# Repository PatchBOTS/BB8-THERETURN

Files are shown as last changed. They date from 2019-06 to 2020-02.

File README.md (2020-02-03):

# BB8-THERETURN
In March 2019 I decided to rebuild my James Bruton V3 BB-8 electronics from the ground up. Here are my Results. 

I've posted the zipped Gerber files for the board. This can be uploading directly to PCBWay.com or other board house for fabrication. 
I've also posted a CSV for the digikey passive components needed to assemble the board.  
Here is a link to the digikey BOM (let me know if this isn't working)
https://www.digikey.com/BOM/Create/CreateSharedBom?bomId=8143564

Notes on Assembly. 
1. To make room on the board I only have through holes for the needed pins on both the Sparkfun Pro Micro and the BY8301-16p.  This means you will NOT be soldering all the pin headers onto the Sparkfun Pro Micro and you will need to CUT pins off of the BY8301-16p.  This also makes it a bit lighter :)
2. There is a built in programming port for the HC-05 module on the board. I recommend soldering the HC-05 module on first and using this programming port to get your Slave Binding address before continuing with assembly. 
3. There is mP3 solder jumper underneath the BY8301-16p labled "mp3 program"  you will need to solder this jumper for the board to work.  You will need to unsolder it to reprogram the mp3 player after installation. 

I Wil update this guide with pictures as soon as possible. Feel free to message me in the meantime with any questions.

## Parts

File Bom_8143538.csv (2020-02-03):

Manufacturer Part Number | Manufacturer | Digi-Key Part Number | Customer Reference | Reference Designator | Packaging | Part Status | Quantity | Unit Price | Extended Price | Quantity Available | Mfg Std Lead Time | Description | RoHS Status | Lead Free Status | REACH Status
L6932H1.2TR | STMicroelectronics | 497-7766-1-ND |  |  | Cut Tape (CT) | Active | 2 | 2.80000 | $5.60 | 7 | 11 Weeks | IC REG LINEAR POS ADJ 2A 8HSO | ROHS3 Compliant | Lead free | REACH Unaffected
C4532JB1C226M200KA | TDK Corporation | 445-11945-1-ND |  |  | Cut Tape (CT) | Active | 4 | 1.30000 | $5.20 | 1376 | 12 Weeks | CAP CER 22UF 16V JB 1812 | ROHS3 Compliant | Lead free | REACH Unaffected
ERJ-12ZYJ104U | Panasonic Electronic Components | P100KWCT-ND |  |  | Cut Tape (CT) | Active | 2 | 0.26000 | $0.52 | 4887 | 13 Weeks | RES SMD 100K OHM 5% 3/4W 2010 | ROHS3 Compliant | Lead free | REACH Unaffected
RC2010JK-071KL | Yageo | YAG3385CT-ND |  |  | Cut Tape (CT) | Active | 2 | 0.21000 | $0.42 | 85407 | 33 Weeks | RES SMD 1K OHM 5% 3/4W 2010 | ROHS3 Compliant | Lead free | REACH Unaffected
RMCF2010JT2K00 | Stackpole Electronics Inc | RMCF2010JT2K00CT-ND |  |  | Cut Tape (CT) | Active | 1 | 0.23000 | $0.23 | 14356 | 17 Weeks | RES 2K OHM 5% 3/4W 2010 | ROHS3 Compliant | Lead free | REACH Unaffected
CRCW20103K30FKEF | Vishay Dale | 541-3.30KACCT-ND |  |  | Cut Tape (CT) | Active | 1 | 0.29000 | $0.29 | 11927 | 12 Weeks | RES SMD 3.3K OHM 1% 3/4W 2010 | ROHS3 Compliant | Lead free | Not Available
ERJ-12ZYJ362U | Panasonic Electronic Components | P3.6KWCT-ND |  |  | Cut Tape (CT) | Active | 1 | 0.26000 | $0.26 | 4770 | 13 Weeks | RES SMD 3.6K OHM 5% 3/4W 2010 | ROHS3 Compliant | Lead free | REACH Unaffected
DEV-12640 | SparkFun Electronics | 1568-1060-ND |  |  | Bulk | Active | 1 | 19.95000 | $19.95 | 234 | 2 Weeks | PRO MICRO ATMEGA32U4 5V/16MHZ | RoHS Compliant | Lead free | Not Available

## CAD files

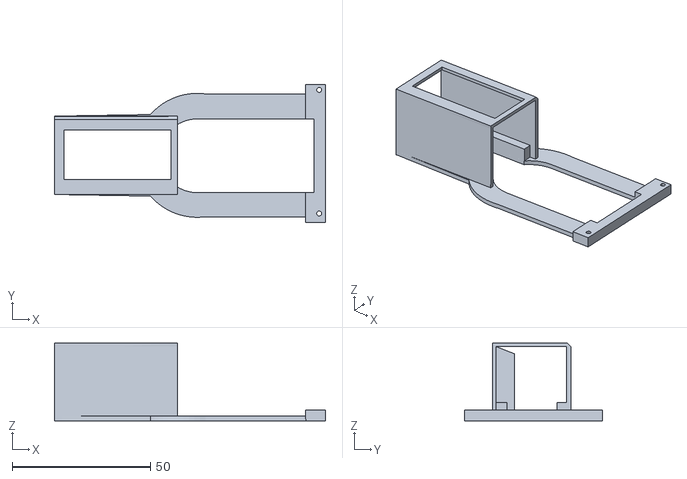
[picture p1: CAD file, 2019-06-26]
InternalSLEDMount.STL
98.0 x 49.7 x 28.0

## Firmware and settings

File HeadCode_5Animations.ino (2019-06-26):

// =======================================================================================
//                         BB-8 Head -- Lights and Sounds
// =======================================================================================
//                            Written By: PatchBOTS
// =======================================================================================
//       Credit and  Major thank you to:  David Scott,  afreeland, and ron_dl
// ---------------------------------------------------------------------------------------
//                     microcontroller  ---  Sparkfun Pro Micro (5v)
// --------------------------------------------------------------------------------------
//
//                                 proMicro
//                                ------------
//                                |           |
//                     +--------------------------------+
//                     |                                |
//                     | [ ]TX                   RAW[ ] |
//              HC-05  | [ ]RX                   GND[ ] |
//                     | [ ]GND                  RST[ ] |
//                     | [ ]GND                  VCC[ ] |
//                     | [ ]2                     A3[ ] |
//               Busy  | [ ]3                     A2[ ] |
//              NeoPix | [ ]4                     A1[ ] |
//               State | [ ]5                     A0[ ] | Audio in
//                     | [ ]6                     15[ ] | SoftSerialTX
//                     | [ ]7                     14[ ] |
//                     | [ ]8                     16[ ] |
//                     | [ ]9                     10[ ] |
//                     |                                |
//                     +--------------------------------+
//
//
// ---------------------------------------------------------------------------------------
//                                   NOTES
// ---------------------------------------------------------------------------------------
//
//SMD HC-05 Bluetooth Module Slave address:  98d3,32,31870f

// -----------------------------------------------------------------------------
//                          Libraries
// -----------------------------------------------------------------------------
#include "MP3FLASH16P.h"
#include <Adafruit_NeoPixel.h>
#include <SoftwareSerial.h>

// -----------------------------------------------------------------------------
//                      Definitions/Variables
// -----------------------------------------------------------------------------

#define mp3busypin 3  // connected to Busy pin on Mp3 Unit
#define AudioIn    A0 //connected to SPK1 on mP3 player
#define neopixel   4  // neopixels out

//**********NeoPixels**************
#define NUMPIXELS      18
Adafruit_NeoPixel pixels = Adafruit_NeoPixel(NUMPIXELS, neopixel, NEO_GRB + NEO_KHZ800);

//*****Arrays for specific NeoLights
int blueLogicArray [] = {0, 1, 2};
int topLogicArray [] = {3, 5, 7};
int bottomLogicArray [] = {4, 6, 8};
int dualLogicArray [] = {3, 4, 5, 6, 7, 8}; //for both top and bottom white logic displays
int dualLogicHoloArray [] = {3, 4, 5, 6, 7, 8, 10}; //for both top and bottom white logics and the hololens
int radarArray [] = {11, 12, 13, 14, 15, 16, 17};
//PSI light is 9
//HoloLens is 10

//**********Serial Input**************
boolean newData = false;
const byte numChars = 32;
char receivedChars[numChars];
char tempChars[numChars];
int trig1 = 1;
int trig2 = 1;
int trig3 = 1;
int trig4 = 1;
int trig5 = 1;
int volumeKnob = 500;
int aniMode = 0;

//**********PSI Light**************
int AudioReading;
int mp3volume;
int voiceBrightness = 0;
int audioUpper;
int audioLower;
int absoluteUpper;
int pulse;

//**********mp3Player**************
MP3FLASH16P myPlayer; //calls the David Scott mp3 library

//**********Timing**************
long previousMillis = 0;        // will store last time sound played was updated
long sound_interval = 15000; //the autonomous sound interval.  15000 = 15 seconds between sounds
int currentMillis = 0;

//*********AnimationVaribales*************************
//GLOBAL
long startTime = 0; //used as a stopwatch for the animations

//Color Variables
uint32_t low = pixels.Color(0, 0, 0); //a simple way of writing "turn this pixel off"
uint32_t neoRed = pixels.Color(255, 0, 0);//a simple way of writing "turn this pixel red"
uint32_t neoBlue = pixels.Color(0, 0, 255);//a simple way of writing "turn this pixel blue"
uint32_t neoWhite = pixels.Color(255, 255, 255);//a simple way of writing "turn this pixel white"
uint32_t voiceBright = pixels.Color(voiceBrightness, voiceBrightness, voiceBrightness); //a simple way of writing "make this pixel match teh voice brightness"
uint32_t voiceBrightRed = pixels.Color(voiceBrightness,0,0); //a simple way of writing "make this pixel match teh voice brightness in a red color"
uint32_t voiceBrightBlue = pixels.Color(0,0,voiceBrightness); //a simple way of writing "make this pixel match teh voice brightness in a Blue color"

//Animation 1
int aniOneInterval = 60; //for single knightriders, time between each lightup
int aniOne_i = 0; //generic holder
int aniOne_iLast = 0;
int aniOneRiderFlag = 3; //this will allow the loops of knightrider scrolls to run sequentially
unsigned long aniOneMillis = 0;  //local stopwatch for Animation 1
long aniOnePreviousMillis = 0; //a ref point for timing
bool aniOneP2 = false; 

//Animation 2
unsigned long aniTwoMillis = 0;  //local stopwatch for Animation 1
bool aniTwoFlag1= false; 
bool aniTwoFlag2= false; 
bool aniTwoFlag3= false;
bool aniTwoFlag4= false;
bool aniTwoFlag5= false; 
int aniTwo_i = 0; //generic holder
int aniTwo_iLast = 0;
int aniTwoRiderFlag = 0; //this will allow the loops of knightrider scrolls to run sequentially
int aniTwoInterval = 60; //for single knightriders, time between each lightup
long aniTwoPreviousMillis = 0; //a ref point for timing

//Animation 3
unsigned long aniThreeMillis = 0;  //local stopwatch for Animation 1
long aniThreePreviousMillis = 0; //a ref point for timing
bool aniThreeFlag = false; 

//Animation 4
unsigned long aniFourMillis = 0;  //local stopwatch for Animation 1
long aniFourPreviousMillis = 0; //a ref point for timing
bool aniFourFlag = false; 

//Animation 5
unsigned long aniFiveMillis = 0;  //local stopwatch for Animation 1
long aniFivePreviousMillis = 0; //a ref point for timing
bool aniFiveFlag = false; 



// -----------------------------------------------------------------------------
//                              SETUP
// -----------------------------------------------------------------------------
void setup() {
  myPlayer.init(mp3busypin);   // Init the player with the busy pin connected to Arduino pin 3
  delay(1000);  // Startup delay
  Serial.begin(9600);  //Start Serial, eventually connecting to HC-05
  Serial1.begin(9600);
  pixels.begin(); // This initializes the NeoPixel library.
  pinMode(AudioIn, INPUT); //set pin to read voltage output
 knightRider();

}
// -----------------------------------------------------------------------------
//                             MAIN LOOP
// -----------------------------------------------------------------------------
void loop() {
  currentMillis = millis();

  serialStuff(); //reads and parses all incoming serial data into integers.  there is an function "showParsedData" which will print to Serial Monitor for debugging

  //**********Volume Knob************************
  mp3volume = map(volumeKnob, 0, 1023, 0, 30); //reads and scales the poteniometer value (0-1023) to a usable mp3 volume (0-30)
  psiLightData (); //this function calculates the light value for the PSI based on the volumeKnob value.

  neoPixels(); //default NeoPixels values for the droid.  Animations will potential update these values before they are shown in the trigModeAni function below
  autoMode(); // This will play a random sound at the desired interval. To change look for "long sound_interval" under "Timing"
  trigMode(); //This will play a sound triggered by the buttons when Animation Mode is not engaged.
  trigModeAni(); //This will play a sound triggered by the buttons with Animations when Animation Mode is engaged.

  aniOne();
  aniTwo();
  aniThree();
  aniFour(); 
  aniFive();

  pixels.show(); // This sends the updated pixel color to the hardware.

}



// -----------------------------------------------------------------------------
//                ADDITIONAL FUNCTIONS (NON ANIMATION)
// -----------------------------------------------------------------------------
//*******Serial***********
void serialStuff () {
  recvWithStartEndMarkers();
  if (newData == true) {
    strcpy(tempChars, receivedChars);
    parseData();
    showParsedData(); //prints incoming data to Serial port. Mainly for debugging
    newData = false;
  }
}

//*******Autonomous Mode***********
void autoMode () {
  if (currentMillis - previousMillis > sound_interval) {
    previousMillis = currentMillis;
    myPlayer.playFile(random(1, 10), mp3volume);
  }
}

//*******Trigger Mode (No Animations)***********
void trigMode () {
  if (aniMode == 0) {
    if ((trig1 == 0) && (!myPlayer.isBusy())) {
      previousMillis = currentMillis;
      myPlayer.playFile(1, mp3volume);
    }
    if ((trig2 == 0) && (!myPlayer.isBusy())) {
      previousMillis = currentMillis;
      myPlayer.playFile(2, mp3volume);
    }

    if ((trig3 == 0) && (!myPlayer.isBusy())) {
      previousMillis = currentMillis;
      myPlayer.playFile(3, mp3volume);
    }
    if ((trig4 == 0) && (!myPlayer.isBusy())) {
      previousMillis = currentMillis;
      myPlayer.playFile(4, mp3volume);
    }
    if ((trig5 == 0) && (!myPlayer.isBusy())) {
      previousMillis = currentMillis;
      myPlayer.playFile(5, mp3volume);
    }
  }
}

//*******Trigger Mode (With Animations)***********
void trigModeAni () {
  if (aniMode == 1) {
    if ((trig1 == 0) && (!myPlayer.isBusy())) {
      myPlayer.playFile(1, mp3volume);
      previousMillis = currentMillis;
      startTimer ();
      aniOneRiderFlag = 0;
      aniOneP2 = true; 
    }
    if ((trig2 == 0) && (!myPlayer.isBusy())) {
      myPlayer.playFile(2, mp3volume);
      previousMillis = currentMillis;
      startTimer ();
      aniTwoFlag1 = true; 
    }
    if ((trig3 == 0) && (!myPlayer.isBusy())) {
      myPlayer.playFile(3, mp3volume);
      previousMillis = currentMillis;
      startTimer ();
      aniThreeFlag = true; 
    }
    if ((trig4 == 0) && (!myPlayer.isBusy())) {
      myPlayer.playFile(4, mp3volume);
      previousMillis = currentMillis;
      startTimer ();
      aniFourFlag = true; 
    }
    if ((trig5 == 0) && (!myPlayer.isBusy())) {
      myPlayer.playFile(5, mp3volume);
      previousMillis = currentMillis;
      startTimer ();
      aniFiveFlag = true; 
    }
  }
}

//*******PSI Data Calculation****************
void psiLightData () {
  if ((volumeKnob >=   0) && (volumeKnob <=  33)) {
    audioUpper = 512; //0
    audioLower = 512;//0
    absoluteUpper = 0;
  }
  if ((volumeKnob >=  34) && (volumeKnob <= 132)) {
    audioUpper = 542; //30
    audioLower = 475; //37
    absoluteUpper = 37;
  }
  if ((volumeKnob >= 133) && (volumeKnob <= 231)) {
    audioUpper = 593; //81
    audioLower = 418; //94
    absoluteUpper = 94;
  }
  if ((volumeKnob >= 232) && (volumeKnob <= 330)) {
    audioUpper = 644; //132
    audioLower = 367; //145
    absoluteUpper = 145;
  }
  if ((volumeKnob >= 331) && (volumeKnob <= 429)) {
    audioUpper = 695; //183
    audioLower = 316; //196
    absoluteUpper = 196;
  }
  if ((volumeKnob >= 430) && (volumeKnob <= 528)) {
    audioUpper = 746; //234
    audioLower = 264; //248
    absoluteUpper = 248;
  }
  if ((volumeKnob >= 529) && (volumeKnob <= 627)) {
    audioUpper = 797; //285
    audioLower = 212; //300
    absoluteUpper = 300;
  }
  if ((volumeKnob >= 628) && (volumeKnob <= 726)) {
    audioUpper = 848; //336
    audioLower = 160; //352
    absoluteUpper = 352;
  }
  if ((volumeKnob >= 727) && (volumeKnob <= 825)) {
    audioUpper = 899; //387
    audioLower = 108; //404
    absoluteUpper = 404;
  }
  if ((volumeKnob >= 826) && (volumeKnob <= 924)) {
    audioUpper = 953; //441
    audioLower = 56; //456
    absoluteUpper = 456;
  }
  if ((volumeKnob >= 925) && (volumeKnob <= 1023)) {
    audioUpper = 1008; //496
    audioLower = 4; //508
    absoluteUpper = 508;
  }
}


//********PSI Light********************
void psiLight() {
  AudioReading = analogRead(AudioIn);
  //I'm using an arbitrary 34 on the volume knob as the lower end. Anything below that value is effectively "off"
  if ((myPlayer.isBusy()) && (volumeKnob >= 34)) { //if the mP3 player is and the volume is over the 34 lower limit
    if ((AudioReading >= 485) && (AudioReading <= 540)) { //there is a little dead zone that has no audible sound, but still makes the light come on, looks weird.
      pixels.setPixelColor(9, pixels.Color(0, 0, 0)); //this says turn the light off in that deadzone.
    }

    else { //otherwise, if not in the dead zone
      voiceBrightness = constrain(map(AudioReading, 512, audioUpper, -10, 300), 0, 255); //map the upper portion of the audio reading (512 through upper limit determined by volume knob) to -10 and 300, and then constrain that to 0-255.  This constraint hacks off some edges that don't help the effect.
      pixels.setPixelColor(9, pixels.Color(voiceBrightness, voiceBrightness, voiceBrightness)); //set PSI light to calculated value
    }
  }
  else { //otherwise if the mp3 player isn't busy or the volume knob isn't greater than 34....
    pixels.setPixelColor(9, pixels.Color(0, 0, 0));//....turn the light off
  }

}

//********HoloLens**************
void holoLens() {
  pulse = 100 + (sin(millis() / 1000.00) * 80); //generates an oscillating sine wave of values
  pixels.setPixelColor(10, pixels.Color(0, 0, pulse)); // writes the value to the Blue channel of the neopixel
}


//********Logics***************
void logics() {
  // Blue Logics
  pixels.setPixelColor(0, pixels.Color(0, 0, 255)); // Set Side Logics to Blue
  pixels.setPixelColor(1, pixels.Color(0, 0, 255)); // Set Side Logics to Blue
  pixels.setPixelColor(2, pixels.Color(0, 0, 255)); // Set Side Logics to Blue

  //Top Logics
  pixels.setPixelColor(3, pixels.Color(200, 200, 200)); // Set Top Logics to White
  pixels.setPixelColor(5, pixels.Color(200, 200, 200)); // Set Top Logics to White
  pixels.setPixelColor(7, pixels.Color(200, 200, 200)); // Set Top Logics to White

  //Bottom Logics
  pixels.setPixelColor(4, pixels.Color(0, 0, 0)); // Set Bottom Logics off
  pixels.setPixelColor(6, pixels.Color(0, 0, 0)); // Set Bottom Logics off
  pixels.setPixelColor(8, pixels.Color(0, 0, 0)); // Set Bottom Logics off
}

//*********SerialStuff*******************
void recvWithStartEndMarkers() {
  static boolean recvInProgress = false;
  static byte ndx = 0;
  char startMarker = '<';
  char endMarker = '>';
  char rc;

  while (Serial1.available() > 0 && newData == false) {
    rc = Serial1.read();

    if (recvInProgress == true) {
      if (rc != endMarker) {
        receivedChars[ndx] = rc;
        ndx++;
        if (ndx >= numChars) {
          ndx = numChars - 1;
        }
      }
      else {
        receivedChars[ndx] = '\0'; // terminate the string
        recvInProgress = false;
        ndx = 0;
        newData = true;
      }
    }
    else if (rc == startMarker) {
      recvInProgress = true;
    }
  }
}

//*********SerialStuff*******************
void parseData() {      // split the data into its parts

  char * strtokIndx; // this is used by strtok() as an index

  strtokIndx = strtok(tempChars, ",");     // get the first part - the string
  trig1 = atoi(strtokIndx);  // convert to an integer (trig1)

  strtokIndx = strtok(NULL, ","); // this continues where the previous call left off
  trig2 = atoi(strtokIndx);     // convert to an integer (trig2)

  strtokIndx = strtok(NULL, ",");
  trig3 = atoi(strtokIndx);

  strtokIndx = strtok(NULL, ",");
  trig4 = atoi(strtokIndx);

  strtokIndx = strtok(NULL, ",");
  trig5 = atoi(strtokIndx);

  strtokIndx = strtok(NULL, ",");
  volumeKnob = atoi(strtokIndx);

  strtokIndx = strtok(NULL, ",");
  aniMode = atoi(strtokIndx);

}

//*********SerialStuff*******************
void showParsedData() {

  Serial.print(trig1);
  Serial.print(",");
  Serial.print(trig2);
  Serial.print(",");
  Serial.print(trig3);
  Serial.print(",");
  Serial.print(trig4);
  Serial.print(",");
  Serial.print(trig5);
  Serial.print(",");
  Serial.print(volumeKnob);
  Serial.print(",");
  Serial.println(aniMode);
}

//*********NeoPixels*******************

void neoPixels () {
  //Radar Light
  pixels.setPixelColor(11, pixels.Color(200, 0, 0)); // Set First Radar light to red
  logics();
  psiLight();
  holoLens();
}



// -----------------------------------------------------------------------------
//               Animation Functinos
// -----------------------------------------------------------------------------

// A timer function that runs in a lot of the animations
void startTimer () {
  startTime = millis();
  return;
}

//BootUp Animation
void knightRider() {
  int krcount = 0;
  int krtimer = 40;


  // Flash Lights
  for (int i = 0; i < 10; i++) { //set number of loops    i < [numberofloops]
    for (krcount = 0; krcount < 5; krcount++) {
      pixels.setPixelColor(radarArray[krcount], neoRed);
      pixels.show();
      delay(krtimer);
      pixels.setPixelColor(radarArray[krcount + 1], neoRed);
      pixels.show();
      delay(krtimer);
      pixels.setPixelColor(radarArray[krcount], low);
      pixels.show();
      delay(krtimer);
    }
    for (krcount = 5; krcount > 0; krcount--) {
      pixels.setPixelColor(radarArray[krcount], neoRed);
      pixels.show();
      delay(krtimer);
      pixels.setPixelColor(radarArray[krcount - 1], neoRed);
      pixels.show();
      delay(krtimer);
      pixels.setPixelColor(radarArray[krcount], low);
      pixels.show();
      delay(krtimer);
    }
  }

  // Turn them off
  for ( int i = 0; i < 6; i++) {
    pixels.setPixelColor(i, low);
    pixels.show();
  }
}
//Sound 1 - Animation

void aniOne () {
  aniOneMillis = millis();

  if (aniOneMillis - startTime > 900) {
    if (aniOneRiderFlag < 3) {
      pixels.setPixelColor(11, low); 
      pixels.show();
      pixels.setPixelColor(radarArray[aniOne_i], neoRed);
      pixels.show();
      if (aniOneMillis - aniOnePreviousMillis > aniOneInterval) {
        aniOnePreviousMillis = aniOneMillis;
        pixels.setPixelColor(11, low); // Set Side Logics to Blue
        pixels.show();
        pixels.setPixelColor(radarArray[aniOne_iLast], low);
        pixels.show();
        aniOne_iLast = aniOne_i;
        aniOne_i += 1;
        if (aniOne_i > 6) {
          aniOne_i = 0;
          aniOneRiderFlag += 1;
        }
      }
    }
  }

  if (aniOneMillis - startTime > 2300 && aniOneP2 == true) {
    pixels.setPixelColor(4, pixels.Color(voiceBrightness, voiceBrightness, voiceBrightness));
    pixels.setPixelColor(6, pixels.Color(voiceBrightness, voiceBrightness, voiceBrightness));
    pixels.setPixelColor(8, pixels.Color(voiceBrightness, voiceBrightness, voiceBrightness));
    pixels.show(); 
  }
  if (aniOneMillis - startTime > 3000 && aniOneP2 == true) {
    aniOneP2 = false;
    return;
  }
}
//Sound 2 - Animation

void aniTwo () {
  aniTwoMillis = millis();

// SOUND STAGE 1  - THIS IS GOING TO REPLICATE THE VOICE BRIGHTNESS ON THE BOTTOM LOGICS
  if (aniTwoMillis - startTime > 100 && aniTwoMillis - startTime < 800 && aniTwoFlag1 ==true){ 
    pixels.setPixelColor(4, pixels.Color(voiceBrightness+50, voiceBrightness+50, voiceBrightness+50));
    pixels.setPixelColor(6, pixels.Color(voiceBrightness+50, voiceBrightness+50, voiceBrightness+50));
    pixels.setPixelColor(8, pixels.Color(voiceBrightness+50, voiceBrightness+50, voiceBrightness+50));
    pixels.show(); 
    aniTwoFlag2 = true; 
  }
 //SOUND GAP 1
  if (aniTwoMillis - startTime >= 800 && aniTwoMillis - startTime < 1250 && aniTwoFlag2 == true){
    pixels.setPixelColor(3, low);
    pixels.setPixelColor(4, low);
    pixels.setPixelColor(5, low);
    pixels.setPixelColor(6, low);
    pixels.setPixelColor(7, low);
    pixels.setPixelColor(8, low);
    pixels.show(); 
    aniTwoRiderFlag =1; 
    aniTwoFlag3 = true; 
  }
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

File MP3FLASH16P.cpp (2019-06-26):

/*
  MP3FLASH16P.h - Library for the MP3 FLASH 16P module
  Created by /u/afreeland
  Released into the public domain
*/

#include "Arduino.h"
#include "SoftwareSerial.h"
#include "MP3FLASH16P.h"
SoftwareSerial MP3Serial(16, 15);//RX/TX


MP3FLASH16P::MP3FLASH16P()
{
}

void MP3FLASH16P::init(int PIN_BUSY, int VOLUME)
{
    _PIN_BUSY = PIN_BUSY;
    _VOLUME = (uint8_t)VOLUME;
    MP3Serial.begin(9600);

    pinMode(_PIN_BUSY, INPUT);
    digitalWrite(_PIN_BUSY, LOW);
    // Serial.begin(2400);
}

void MP3FLASH16P::playFile(int FILE_NUMBER, int VOLUME)
{
    if(VOLUME != -1)
    {
        _VOLUME = (uint8_t)VOLUME;
    }

    setVolume(_VOLUME);

    delay(100);
    uint8_t filenumber = (uint8_t)FILE_NUMBER;
    // PDF example of how to play first track
    //uint8_t play1[7] = { 0X7E, 0X05, 0X41, 0X00, 0X01, 0X45, 0XEF };

    // param[1] Op Code - Determines what action is caused
    // param[2] High Track - No clue
    // param[3] Low Track - The file that we want to play
    uint8_t play_params[3] = { 0X41, 0X00, filenumber };
    int arrSize = sizeof(play_params)/sizeof(uint8_t);
    uint8_t * _params = buildParams(play_params, arrSize);

    makeRequest(_params, arrSize);

}

void MP3FLASH16P::playFileAndWait(int FILE_NUMBER, int VOLUME)
{
    playFile(FILE_NUMBER, VOLUME);
    delay(100);
    while(isBusy()){
    }
    delay(250);
}

bool MP3FLASH16P::isBusy()
{
  // The BUSY pin will be HIGH while playing and LOW when stopped
  // So we need to check if our busy pin is HIGH, if so it is playing, therefor, is busy
    return digitalRead(_PIN_BUSY) == HIGH;
}

uint8_t * MP3FLASH16P::buildParams(uint8_t *params, int len)
{
  // Since we cant easily set dynamic array length, and even if we
  // did it can cause the 'heap' to become fragmented...we will simply default to a max of 10
  // http://arduino.stackexchange.com/questions/3774/how-can-i-declare-an-array-of-variable-size-globally
  // http://arduino.stackexchange.com/questions/682/is-using-malloc-and-free-a-really-bad-idea-on-arduino
  //uint8_t payload[10] = { (uint8_t)len };
  uint8_t* payload = new uint8_t[10];

  // Set the Length to user params + 2
  // params.length + Length arg + Checksum arg
  payload[0] = (uint8_t)(len + 2);

  // Create our the beginning of our calculated checksum..the first part is our length argument
  uint8_t checksum = payload[0];

  // Build out our full payload while also
  // calculating out our checksum
  for (int i=0; i<len; i++)
  {
      // We need to XOR the current parameter with our current checksum
      checksum = (checksum ^ params[i]);

      payload[(i + 1)] = params[i];
  }

  payload[len+1] = checksum;

  for(int z = 0; z < 10; z++){
    if(z > len + 1){
      // our current iteration is larger than the params passed in, lets start zeroing out
      payload[z] = 0x99;
    }else{
      //Serial.println(payload[z], HEX);
    }
  }

  return (uint8_t *)payload;
}

void MP3FLASH16P::setVolume(int VOLUME)
{
    _VOLUME = constrain(VOLUME, 0, 30);

    //uint8_t volume_op[6]  = {0X7E, 0X04, 0X31, 0X19, 0X2C, 0XEF };
    uint8_t volume_op[2]  = {0X31, _VOLUME};
    int arrSize = sizeof(volume_op)/sizeof(volume_op[0]);
    uint8_t * _params = buildParams(volume_op, arrSize);

    makeRequest(_params, arrSize);

}

void MP3FLASH16P::makeRequest(uint8_t * params, int len)
{
  // Write our start code
    MP3Serial.write((uint8_t)0X7E);

    // Write parameters while building checksum
    for (int i=0; i < len + 2; i++)
    {
      if(params[i] == 0x99)
        break;

      //Serial.println(params[i], HEX);
        // Write our current parameter
        MP3Serial.write( (uint8_t)params[i] );
    }

    // Write our end code
    MP3Serial.write((uint8_t)0XEF);
}

void MP3FLASH16P::volumeUp()
{
    _VOLUME = min(_VOLUME+5, 30);
}

void MP3FLASH16P::volumeDown()
{
    _VOLUME = max(_VOLUME-5, 0);
}

void MP3FLASH16P::stopPlay()
{
    uint8_t play1[8] = { 0X7E, 0XFF, 0X06, 0X16, 0X00, 0x00, 0x00, 0XEF };
    for (int i=0; i<8; i++)
    {
        MP3Serial.write( play1[i] );
    }
}
